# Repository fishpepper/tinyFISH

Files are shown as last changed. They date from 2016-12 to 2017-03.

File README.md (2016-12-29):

# tinyFISH -- tiny / light / f3 / integrated receiver

My approach to build a small and lightweight flight controller.

See [http://fishpepper.de/projects/tinyFISH](http://fishpepper.de/projects/tinyFISH) for more details.

tinyFISH image

This thing is TINY! The outer dimensions are 20x20mm with a 16mm hole-to-hole spacing.
It runs betaflight and includes a FrSky compatible RX, a current- and
voltage-sensor, a blackbox logger, and it is open hardware -- go and build one yourself!

Key features:
- STM32F303 CPU
- MPU6000 gyro (SPI connection!)
- integrated FrSky compatible rx based on [uSKY](http://fishpepper.de/projects/uSKY)
- integrated current- and voltage sensor
- integrated blackbox logger
- betaflight ready

This work is published under the CERN open hardware license v1.2. 
Feel free to use the design - but make sure to give proper credit 
and release all modifications under the same license! 
See LICENSE.txt for details!

THIS COMES WITH NO WARRANTY! BUILD, FLY, AND USE AT YOUR OWN RISK!

# Build your own

Make sure to init the git submodule for the libraries in the
kicad_misc directory by calling git submodule init && git submodule update.
You will have to use a recent kicad version, i used the commit #efdfaeb
when i designed this circuit board. Older versions will probably not work.

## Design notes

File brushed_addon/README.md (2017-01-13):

brushless_addon for tinyFISH FC -- convert your tinyFISH fc to brushed

this tiny add-on board will convert the tinyFISH fc into a brushed FC

this is open hardware - see LICENSE for details

THIS COMES WITH NO WARRANTY! BUILD AND USE AT YOUR OWN RISK!

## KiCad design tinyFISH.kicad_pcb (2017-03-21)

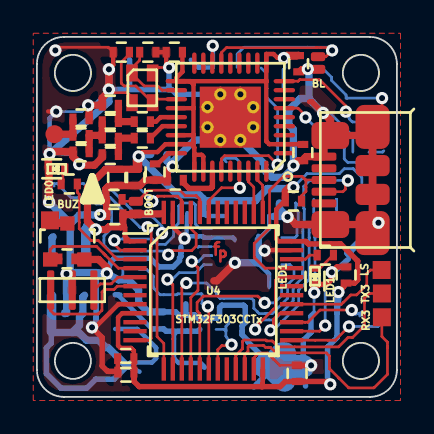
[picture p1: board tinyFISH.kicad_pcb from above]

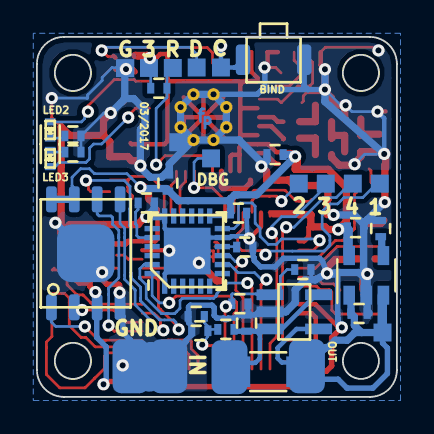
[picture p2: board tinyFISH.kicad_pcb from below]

Board: 2 copper layers, 20.0 x 20.0 mm, 87 parts (40 on the bottom side), 56 nets.

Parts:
ANT1: TP; smd_1x1_round
BIND1: CUSTOM_PUSHBUTTON; OMRON_B3U-3000P
BL1: BL; SOLDERBRIDGE
C1, C10, C17, C23: 1u; C_0402_CUSTOM
C2, C6: 12p; C_0402_CUSTOM
C3, C13, C14, C16, C19, C20, C21, C22, C25, C26, C27, C29: 100n; C_0402_CUSTOM
C4, C7: 100p; C_0402_CUSTOM
C5: 220p; C_0402_CUSTOM
C8, C9: 1p; C_0402_CUSTOM
C11: 1p8; C_0402_CUSTOM
C12: 1p5; C_0402_CUSTOM
C15: 2n2; C_0402_CUSTOM
C18: 4u7; C_0402_CUSTOM
C24, C30: 10n; C_0402_CUSTOM
C28: NC; C_0402_CUSTOM
DEBUG1: TP; TP_1x1
GND_IN1: GND; PAD_2x3
GND_MOUNT_2: GND; TP_1x1
GND_OUT1: GND; PAD_2x3
H1, H2, H3, H4: hole; mouting_hole
ISP_3V1: TP; TP_1x1
ISP_CLOCK1: TP; TP_1x1
ISP_DATA1: TP; TP_1x1
ISP_GND1: TP; TP_1x1
JP0: BOOT0; SOLDERBRIDGE
L1, L2, L3: 1.2nH; L_0402_CUSTOM
LED0: BLUE; LED_0402
LED1, LED3: RED; LED_0402
LED2: GREEN; LED_0402
Q1: SI2302DS; SI2302DS_SOT-23
R1, R5, R10: 10k; R_0402_CUSTOM
R3: 56k; R_0402_CUSTOM
R4: 220; R_0402_CUSTOM
R6, R8: 330; R_0402_CUSTOM
R7: 100; R_0402_CUSTOM
R9: 1k5; R_0402_CUSTOM
R11, R501: 1k; R_0402_CUSTOM
R12: 0R005; R_1206
R13: 30k; R_0402_CUSTOM
TP_1: WS2812; TP_1x1
TP_2: UART3_RX; TP_1x1
TP_3: UART3_RX1; TP_1x1
TP_4: BUZZER_GND; TP_1x1
TP_5: BUZZER_VCC; TP_1x1
TP_ESC_0: ESC_0; TP_1x1
TP_ESC_1: ESC_1; TP_1x1
TP_ESC_2: ESC_2; TP_1x1
TP_ESC_3: ESC_3; TP_1x1
U1: CC2510; QFN36_CC2510
U2: MPU-6000; QFN-24
U3: LP2985AIM5-3.0/NOPB; SOT-23-5
U4: STM32F303CCTx; LQFP-48_7x7mm_Pitch0.5mm
U5: M25P16-VME; VFDFPN8
U6: MICRO_USB_B; USB_MICRO_MOLEX
U7: INA139; DBV
VBAT1: CONN_1; PAD_2x3
VBAT_IN1: CONN_1; PAD_2x3
X1: 26MHz; crystal_2016
X2: 8MHz; CSTCE_G_A

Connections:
3V: C3.1, C5.1, C10.1, C13.1, C16.2, C18.1, C19.1, C20.1, C21.1, C22.1, C23.1, C24.1, C25.1, C29.1, ISP_3V1.1, JP0.1, R5.1, R9.1, U1.2, U1.10, U1.19, U1.22, U1.25, U1.26, U1.28, U1.29, U2.13, U3.5, U4.1, U4.9, U4.24, U4.36, U4.48, U5.3, U5.7, U5.8
/power/BAT+: C26.2, R10.2, R12.1, U7.3, U7.5, VBAT_IN1.1
/rx/ANT_N: C4.1, U1.24
/rx/ANT_P: C7.1, U1.23
/rx/ISP_CLOCK: BIND1.1, ISP_CLOCK1.1, U1.16
/rx/ISP_DATA: BL1.1, ISP_DATA1.1, U1.15
/rx/~RESET: R5.2, U1.31
ADC_CURRENT: C28.2, R13.1, U4.18, U7.1
ADC_VBAT: C27.1, R10.1, R11.2, U4.19
BUZZER: Q1.D, TP_4.1
BUZZER_IO: Q1.G, R501.2, U4.4
ESC_0: TP_ESC_0.1, U4.45
ESC_1: TP_ESC_1.1, U4.46
ESC_2: TP_ESC_2.1, U4.13
ESC_3: TP_ESC_3.1, U4.12
FLASH_CS: U4.25, U5.1
FLASH_MISO: U4.27, U5.2
FLASH_MOSI: U4.28, U5.5
FLASH_SCK: U4.26, U5.6
GND: BIND1.2, BL1.2, C1.1, C2.2, C3.2, C5.2, C6.2, C8.1, C10.2, C11.1, C12.1, C13.2, C14.2, C15.1, C16.1, C17.2, C18.2, C19.2, C20.2, C21.2, C22.2, C23.2, C24.2, C25.2, C26.1, C27.2, C28.1, C29.2, C30.2, GND_IN1.1, GND_MOUNT_2.1, GND_OUT1.1, ISP_GND1.1, L1.1, LED0.1, LED1.1, Q1.S, R1.2, R3.1, R4.2, R6.2, R11.1, R13.2, R501.1, U1.GND, U2.1, U2.11, U2.18, U3.2, U4.8, U4.23, U4.35, U4.47, U5.4, U6.5, U7.2, X1.2, X1.4, X2.2
LED_0: R7.1, U4.3
LED_1: R8.1, U4.34
MPU_EXTI: U2.12, U4.2
MPU_SPI_CS: U2.8, U4.14
MPU_SPI_MISO: U2.9, U4.16
MPU_SPI_MOSI: U2.24, U4.17
MPU_SPI_SCK: U2.23, U4.15
unnamed: ANT1.1, C12.2, L3.2
unnamed: C1.2, U1.30
unnamed: C2.1, U1.20, X1.1
unnamed: C4.2, C9.1, L1.2
unnamed: C6.1, U1.21, X1.3
unnamed: C7.2, C8.2, L2.1
unnamed: C9.2, C11.2, L2.2, L3.1
unnamed: C14.1, U2.10
unnamed: C15.2, U2.20
unnamed: C30.1, U3.4
unnamed: JP0.2, R1.1, U4.44
unnamed: LED0.2, R7.2
unnamed: LED1.2, R8.2
unnamed: LED2.1, R4.1
unnamed: LED2.2, U1.9
unnamed: LED3.1, R6.1
unnamed: LED3.2, U1.6
unnamed: R3.2, U1.27
unnamed: R9.2, U4.33, U6.3
unnamed: U4.5, X2.1
unnamed: U4.6, X2.3
unnamed: U4.32, U6.2
RX_DEBUG: DEBUG1.1, U1.33, U4.43
RX_HUB_TELEMETRY: U1.35, U4.37
RX_SBUS: U1.34, U4.38
UART3_RX: TP_3.1, U4.22
UART3_TX: TP_2.1, U4.21
VBAT: C17.1, R12.2, TP_5.1, U3.1, U3.3, U7.4, VBAT1.1
WS2812: TP_1.1, U4.29

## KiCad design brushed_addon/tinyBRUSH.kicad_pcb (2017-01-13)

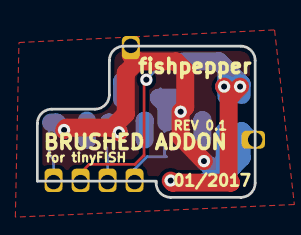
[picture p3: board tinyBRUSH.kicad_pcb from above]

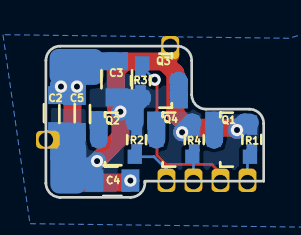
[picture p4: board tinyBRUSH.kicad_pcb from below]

Board: 2 copper layers, 12.1 x 8.4 mm, 24 parts (18 on the bottom side), 10 nets.

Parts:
C2, C3, C4, C5: 47u; C_0805
Q1, Q2, Q3, Q4: FET_N; SI2302DS_SOT-23
R1, R2, R3, R4: 10k; R_0402
TP1: ESC_0; edge_conn_1mm
TP2: ESC_1; edge_conn_1mm
TP3: ESC_2; edge_conn_1mm
TP4: ESC_3; edge_conn_1mm
TP5: M-_0; TP_1x1
TP6: M-_1; TP_1x1
TP7: M-_2; TP_1x1
TP8: M-_3; TP_1x1
TP9: VBAT; PAD_2x3
TP10: GND; PAD_2x3
TP11, TP12: GND; edge_conn_1mm

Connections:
GND: C2.2, C3.2, C4.2, C5.2, Q1.S, Q2.S, Q3.S, Q4.S, R1.2, R2.2, R3.2, R4.2, TP10.1, TP11.1, TP12.1
unnamed: C2.1, C3.1, C4.1, C5.1, TP9.1
unnamed: Q1.D, TP5.1
unnamed: Q1.G, R1.1, TP1.1
unnamed: Q2.D, TP6.1
unnamed: Q2.G, R2.1, TP2.1
unnamed: Q3.D, TP7.1
unnamed: Q3.G, R3.1, TP3.1
unnamed: Q4.D, TP8.1
unnamed: Q4.G, R4.1, TP4.1

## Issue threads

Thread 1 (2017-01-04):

Kicad problem, missing resources?

jimmyw, 2017-01-04:
I was trying to open and view the schema, and was met with this:

```
The following libraries were not found:
tinyFISH-rescue
special
```

If i try open the pcb layout i get this:

```
Error loading board.
KiCad was unable to open this file, as it was created with a more recent version than the one you are running. To open it, you'll need to upgrade KiCad to a more recent version.

Date of KiCad version required (or newer): 2016-08-15

Full error text:
PARSE_ERROR: Expecting 'clearance, trace_width, via_dia, via_drill, uvia_dia, uvia_drill, or add_net' in input/source
'/Users/jimmy/tinyFISH/tinyFISH.kicad_pcb'
line 199
offset 6
from /Users/ansible/4.0.5/kicad-mac-packaging-4.0.0/kicad/common/dsnlexer.cpp : Expecting() : line 369
```

I have not been using kicad before, just curious how your schemetics looks like.

I am using kicad 4.0.5 on mac.

fishpepper, 2017-01-04:
I accidently edited the files when i was binaries compiled from kicad master...
You will need a more recent version from kicad. I compiled my own binaries from kicad commit efdfaeb.

vcazan, 2017-03-13:
I am having troubles building kicad, is there any way you can release some gerbs so I can order from pcbway?

Closed 2017-01-13.

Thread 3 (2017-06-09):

schematic

silver13, 2017-06-09:
Sorry to be annoying by using issues, but is there a schematic in jpg/pdf format?

I installed KiCad but that did not open the files correctly, something about version.

Additionally, do you know of a reception issue, seems to happen most at about half throttle so I assume it's caused by noise (from escs) affecting the receiver chip, which is why I need the schematic.

Thanks for your great work.

TinYOneGit, 2017-06-10:
@silver13
You may want to try the KiCad nightly build (kicad-r8145.d37a33723-x86_64.exe), I had issue opening the files when using the stable build (kicad-4.0.6-x86_64).

Also remember to get a copy of the kicad_misc folder from the repository (i.e. git submodule init; git submodule update)

silver13, 2017-06-11:
Cool, I can see it now, thanks.

What range is the rx supposed to have, I haven't used frsky before...

silver13, 2017-06-18:
I think I figured out the reason for rx issues, it's caused by the vreg. It's pnp based, of the type where the input should be always higher compared to the output. Because it has a diode across.

When escs draw current and voltage drops, it make the diode conduct, which disrupts regulation.

Should be fixable by different regulator type ( fet based ldo)

Anyway, just in case you didn't know.

Closed 2017-06-18.

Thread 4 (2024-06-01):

Possible to get an ELRS version?

sixtyfive, 2024-06-01:
Hi, would it be possible to replace the FRSky receiver on this board with an ELRS one?

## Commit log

2016-12-29 initial release
    [cpu.sch, mpu.sch, power.sch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]
2016-12-30 fixed datestamp
    [tinyFISH.kicad_pcb]
2017-01-10 added bind button
    [cpu.sch, mpu.sch, power.sch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]
2017-01-10 rev 02 oshpark job
    [tinyFISH.kicad_pcb]
2017-01-10 updated doc
    [tinyFISH.kicad_pcb]
2017-01-13 some cosmetic cleanup, fixed esc4 naming
    [tinyFISH.kicad_pcb]
2017-01-13 added omron switch to lib
2017-01-13 added brushed addon board
    [tinyBRUSH.kicad_pcb, tinyBRUSH.sch]
2017-01-15 swapped blue and red led
    [cpu.sch, mpu.sch, power.sch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]
2017-01-16 cleanup and added 3d shapes
    [tinyFISH.kicad_pcb]
2017-02-05 added border
    [tinyFISH.kicad_pcb]
2017-02-21 cleanup to custom r and c parts
    [cpu.sch, mpu.sch, power.sch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]
2017-03-21 fixed rev id
    [tinyFISH.kicad_pcb]
2017-03-21 fixed naming of pads
    [cpu.sch, tinyFISH.kicad_pcb]
2017-03-21 fixed vreg
    [cpu.sch, mpu.sch, power.sch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]
2017-03-21 fixed doc
    [tinyFISH.kicad_pcb]
2017-03-21 fixed doc for esc
    [tinyFISH.kicad_pcb]
